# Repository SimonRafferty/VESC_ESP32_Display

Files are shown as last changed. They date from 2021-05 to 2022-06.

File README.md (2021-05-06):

# VESC_ESP32_Display
This is just a simple display of Speed, Battery Percentage, Power being delivered to the motor and battery voltage on the nice little TTGO Display boards which you can pick up for about $10.

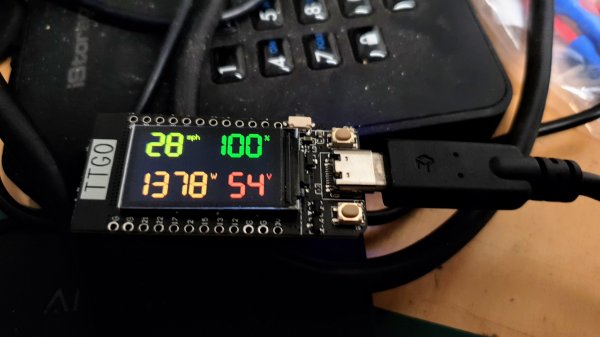
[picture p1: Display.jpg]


The TTGO Board is based on the ESP32 architecture with WiFi, Bluetooth etc but has a very nice, IPS TFT Display on board.  For the price, they are unbeatable!

I've included a 3D Printed case, intended to mount to bicycle Handlebars.  The case could be a lot smaller - but it suited my arrangement.
The top two layers of the case, sandwich a piece of clear plastic. I cut a bit out of one of those crystal boxes you get assortments of components in.  Once you've configured the settings, seal the three layers of the case together with Silicone Mastic and it will be waterproof.  If you want to be able to dismantle it after sealing, spread a thin layer of mastic on the mating surfaces of the bottom two layers and allow them to cure.  The screws provide enough clamping force to seal decently.

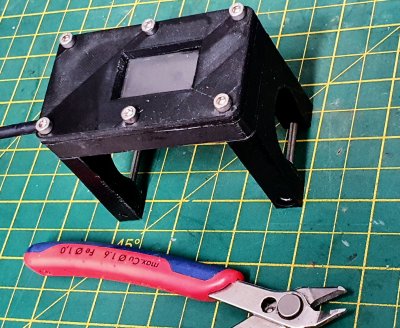
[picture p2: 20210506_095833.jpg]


To connect to the VESC, the Tx & Rx UART connections connect to pins 26 & 25 on the ESP32 respectively.
The Hardware Serial UART pins on the ESC32 are configured in the code (line 61) so you can use whicever pins are most convenient.
+5V & 0V on the VESC to +5v & GND on the ESP32

Ping me an email if you have any queries - I'm happy to answer.

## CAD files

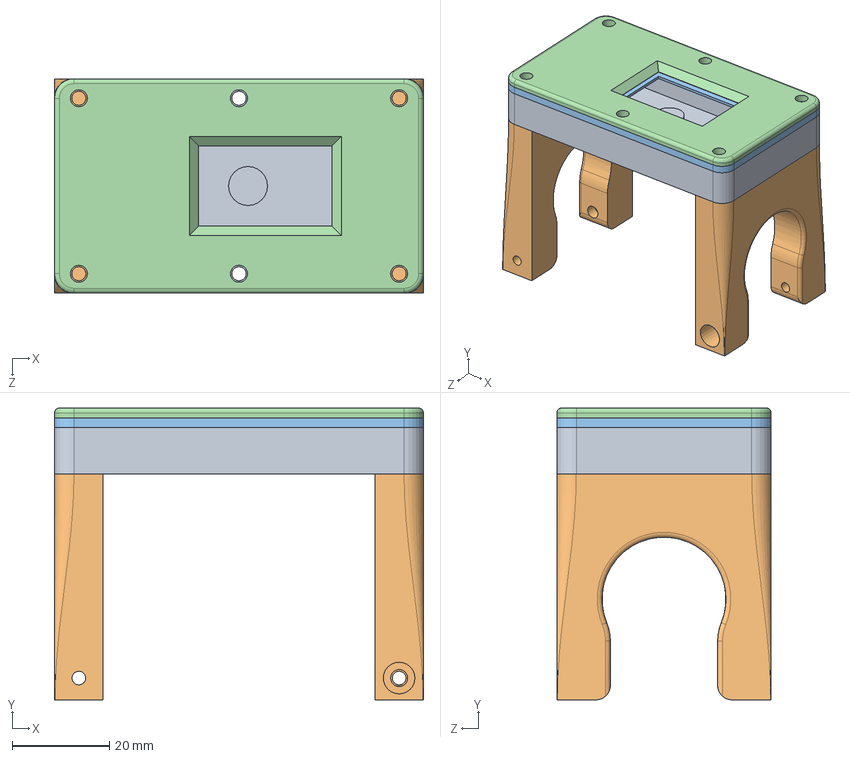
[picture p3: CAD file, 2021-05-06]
VESC Display Case.SLDASM
75.7 x 59.9 x 44.0 mm
Display Bottom
Handlebar Mount x 2
Display Top
Display TTop

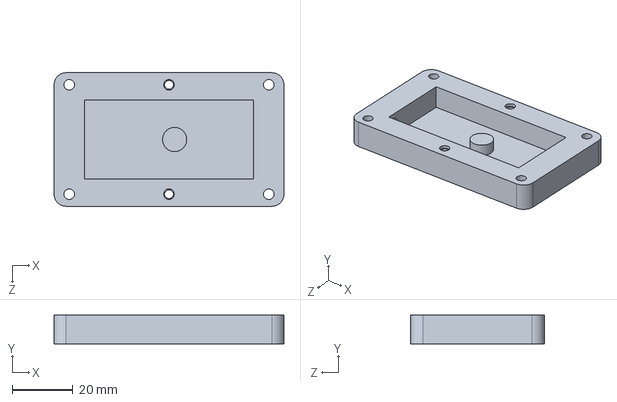
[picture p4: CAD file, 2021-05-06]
Display Bottom.SLDPRT
75.7 x 9.50 x 44.0 mm

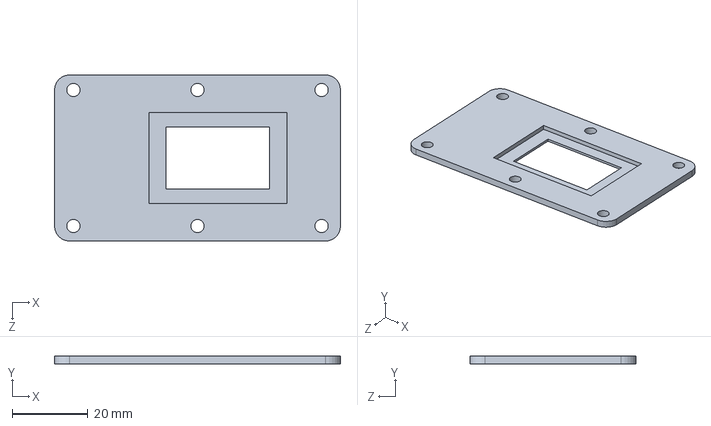
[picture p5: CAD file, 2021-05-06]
Display Top.SLDPRT
75.7 x 2.00 x 44.0 mm

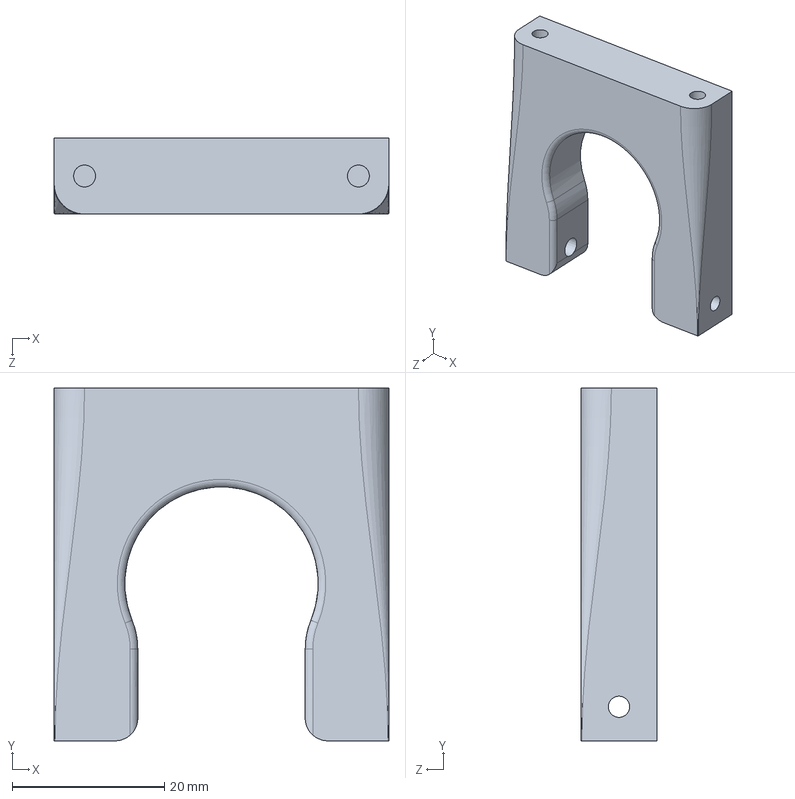
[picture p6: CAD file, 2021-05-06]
Handlebar Mount.SLDPRT
44.0 x 46.4 x 10.0 mm

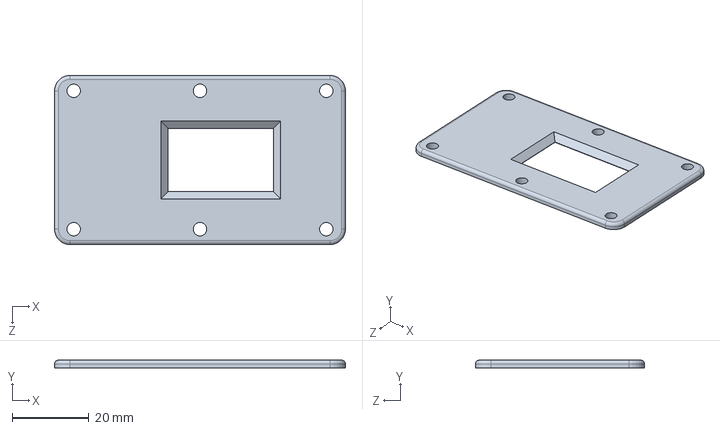
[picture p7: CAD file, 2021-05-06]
Display TTop.SLDPRT
75.7 x 2.00 x 44.0 mm

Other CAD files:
Display Bottom.STL
Display TTop.STL
Display Top.STL
Handlebar Mount.STL

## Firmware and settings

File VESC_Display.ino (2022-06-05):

/*
This code is used to gather data from a VESC6 and display on a colour TFT screen.
Written for TTGO-Display
Board: ESP32 Dev
Based on code by Tom Stanton https://www.youtube.com/watch?v=7jBlKI7aqZA
Who based his on VESCUART.h code written by SolidGeek.
 */


//TFT colors
#define Black 0x0000
#define White 0xFFFF
#define Light_Gray 0xBDF7
#define Dark_Gray 0x7BEF
#define Red 0xF800
#define Yellow 0xFFE0
#define Orange 0xFBE0
#define Brown 0x79E0
#define Green 0x7E0
#define Cyan 0x7FF
#define Blue 0x1F
#define Pink 0xF81F
//TFT Resolution
#define Disp_H 240
#define Disp_V 150


#include <VescUart.h>
#include <SimpleKalmanFilter.h>

#include <TFT_eSPI.h> // Graphics and font library for ST7735 driver chip
#include <SPI.h>

TFT_eSPI tft = TFT_eSPI();  // Invoke library, pins defined in User_Setup.h


/** Initiate VescUart class */
VescUart UART;

//Change these values to suit your setup
int Poles = 46;                  //Usually 46 for hub motor
float WheelDia = 0.51;           //Wheel diameter in m
float GearReduction = 1;         //reduction ratio. 1 for direct drive. Otherwise motor pulley diameter / Wheel pulley diameter.
float BatteryCells = 13;         //Number of cells in Battery


float rpm;
float voltage;
float current;
int power;
float amphour;
float tach;
float distance;
float velocity;
float watthour;
float batpercentage;

SimpleKalmanFilter Filter1(2, 2, 0.01);



void setup() {

  /** Setup Serial port to display data */
  // Serial.begin(9600);

  /** Setup UART port On TTGO Display, you have to assign the pins. 25(Tx) 26(Rx) in this case */
  //** Default VESC brate is 115200, you can change it to any other value. */
  Serial2.begin(115200, SERIAL_8N1, 25, 26);
  /** Define which ports to use as UART */
  UART.setSerialPort(&Serial2);

  tft.init();
  tft.setRotation(1);
  tft.fillScreen(TFT_BLACK);

  tft.setTextColor(Orange); // Note: the new fonts do not draw the background colour

  //Splash Screen
  tft.drawCentreString("Bike belongs to", Disp_H/2, 10, 4);
  tft.drawCentreString("Your Name", Disp_H/2, 45, 4);
  tft.setTextColor(Yellow);
  tft.drawCentreString("Your Phone No", Disp_H/2, 90, 4);



  delay(5000);
  tft.fillScreen(TFT_BLACK);

}
void loop() {
////////// Read values //////////
 if ( UART.getVescValues() ) {
  rpm = UART.data.rpm / (Poles / 2);                                // UART.data.rpm returns cRPM.  Divide by no of pole pairs in the motor for actual.
  voltage = (UART.data.inpVoltage);                                 //Battery Voltage
  current = (UART.data.avgInputCurrent);                            //Current Draw
  power = voltage*current;
  amphour = (UART.data.ampHours);                                   //This doesn't seem to do anything!
  watthour = amphour*voltage;                                       //Likewise
  distance = rpm*3.142*(1.0/1609.0)*WheelDia*GearReduction;         // Motor RPM x Pi x (1 / meters in a mile or km) x Wheel diameter x (motor pulley / wheelpulley)
  velocity = rpm*3.142*(60.0/1609.0)*WheelDia*GearReduction;        // Motor RPM x Pi x (seconds in a minute / meters in a mile) x Wheel diameter x (motor pulley / wheelpulley)
  batpercentage = (voltage-(3.0*BatteryCells)/BatteryCells)*100;   // Based on a minimum of 3V per cell

  /*
  //Debug
  Serial.print("RPM="); Serial.print(rpm);
  Serial.print("|V="); Serial.print(voltage);
  Serial.print("|I="); Serial.print(current);
  Serial.print("|Ah="); Serial.print(amphour);
  Serial.print("|Vel-"); Serial.print(velocity);
  Serial.print("|Dist-"); Serial.print(distance);
  Serial.println();
  */

////////// Filter //////////
  // calculate the estimated value with Kalman Filter
  float powerfiltered = Filter1.updateEstimate(power);



///////// Adjust the below to show apparently legal values //////////
  //if(velocity>10) velocity = (velocity-10)/3+10  //Accurate 0-10mph, reduced 10-15mph so max 25mph shows as 15mph
  //powerfiltered = powerfiltered / 6 //Read 0 to 250W



////////// LCD //////////

// First line

  // tft.fillScreen(TFT_BLACK);
  tft.setTextColor(Orange, Black); // Note: the new fonts do not draw the background colour
  tft.drawRightString(String(int(velocity)), 80, 3, 7);
  tft.drawString("mph", 85, 3, 2);

  //Change Battery Percentage colour based on value
  tft.setTextColor(Red, Black);
  if(batpercentage>30) tft.setTextColor(Orange);
  if(batpercentage>50) tft.setTextColor(Yellow);
  if(batpercentage>80) tft.setTextColor(Green);

  //tft.setTextColor(Yellow); // Note: the new fonts do not draw the background colour
  tft.drawRightString(String(int(batpercentage)), 220, 3, 7);
  tft.drawString("%", 223, 3, 2);


// Second line
  tft.setTextColor(Green, Black); // Note: the new fonts do not draw the background colour
  tft.drawRightString(String(int(powerfiltered)), 120, 80, 7);
  tft.drawString("W", 132, 80, 2);

  tft.setTextColor(Red, Black); // Note: the new fonts do not draw the background colour
  tft.drawRightString(String(int(voltage)), 225, 80, 7);
  tft.drawString("V", 228, 80, 2);
  }
  else
  {
  // tft.fillScreen(TFT_BLACK);
  tft.setTextColor(Orange, Black); // Note: the new fonts do not draw the background colour
  tft.drawCentreString("No Data!", Disp_H/2, 10, 4);


  }

  //To reduce screen flicker, increase value.
  //I ought to re-write it so it draws over the rext in black, which would flicker much less
  delay(500);

}
